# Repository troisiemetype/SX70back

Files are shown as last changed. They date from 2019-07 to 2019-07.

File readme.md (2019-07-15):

# SX70 back

## This Arduino sketch is for managing a SX70 instant film back.

The back is made of a SX70 which only the ejection mecanism was used.
It's included in a wooden enclosure made to fit a Busch Pressman C 3.5x4.5 press camera.

The mecanism includes motor, original switches, gear train. The shutter, bellows, mirror, and original enclosure has been removed, as well as the picture counter, which has been embbeded in the arduino program.

More informations about the functions, switches management, etc. in the .ino file.

### Be kind :

If you use this code and files for a project, consider letting me know, drop a line : lelabodu troisieme (at) gmail.com. Pictures will be welcome, and a donation as well ! :)

### About 3D files :

The STL for the back are included in the STL folder.

*Inner frame* is the only part to be 3D printed, all the enclosure is made of wood, and trigger button and door latch made of brass. They probably can be 3D printed too.

*Main shell* has holes for 3mm leds. On mine the small holes have been filed with clear PU resin.

*Door shell* is composed of several parts assembled, there is an inside slot for mounting a "light tongue", altough maybe not sctrictly necessary.

### About Arduino and electronics :

The flex circuit has been removed from the back chassis. Switches have been connected to ground, and to Arduino using internal pull-up resistors. S3 and S5 (see SX70 repair manual) are used to detect different ejections steps. S7 is the main power switch, which closes and powers the system when a pack is inserted and the door closed. The Arduino is powered as long as there is a pack, but is put asleep after 20 seconds (can be modified) idle.

An Arduino pro-mini has been used, it's placed in a 2mm thick recess in the inside of the main shell near the leds, and simply mounted with double-side tape

### The program uses two libraries :

#### Push button
https://github.com/troisiemetype/PushButton
Simplifies the switches and button management, by providing functions to update, debounce short and long clic, etc. Once a button / switch is created, it just have to be updated as soon as possible (polled in the main loop), and tested whenever needed)

#### Timer
https://github.com/troisiemetype/Timer
Timer made from millis() core Arduino function, with convenient functions for setting times, make loops, etc. Non blocking.

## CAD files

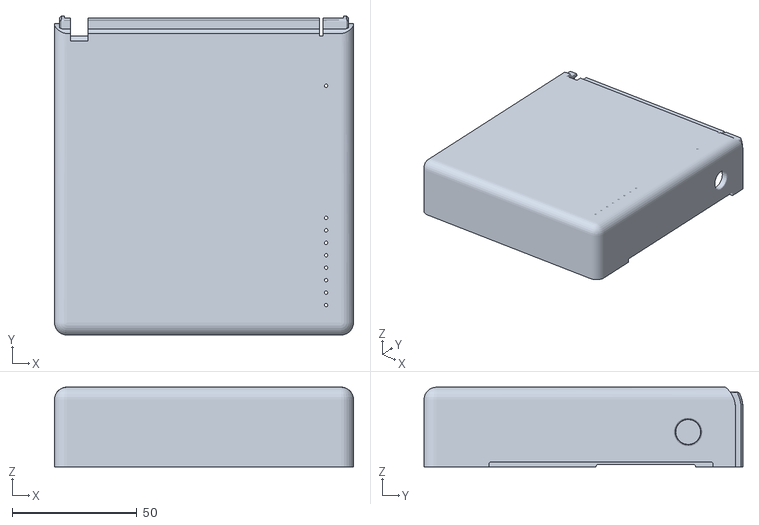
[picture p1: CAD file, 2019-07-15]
stl/pola - main shell.stl
120.0 x 128.0 x 32.0

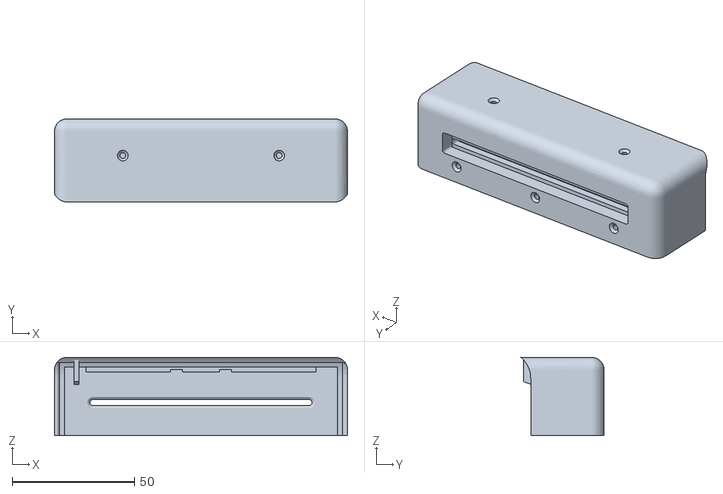
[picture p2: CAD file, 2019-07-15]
stl/pola - door shell.stl
120.0 x 34.0 x 32.0

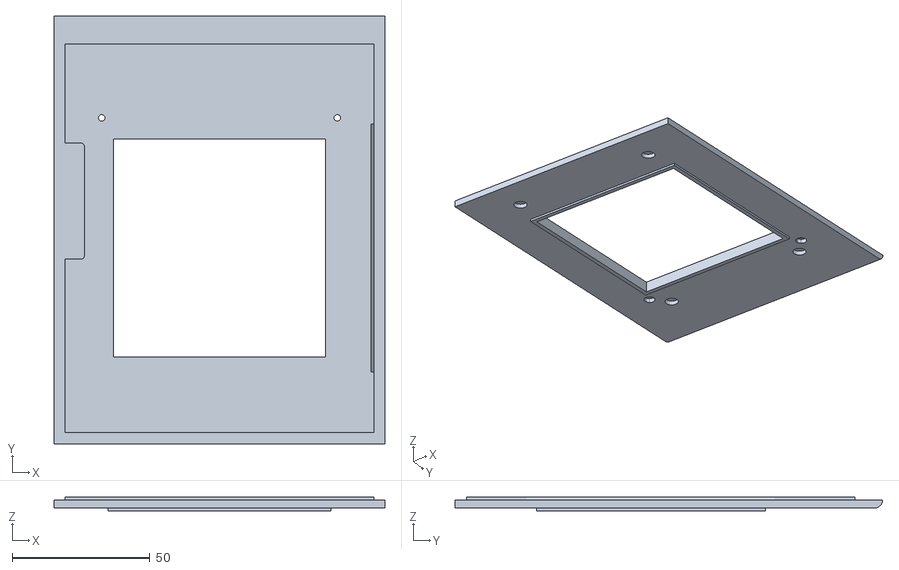
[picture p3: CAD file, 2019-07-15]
stl/pola - base.stl
120.0 x 155.0 x 5.00

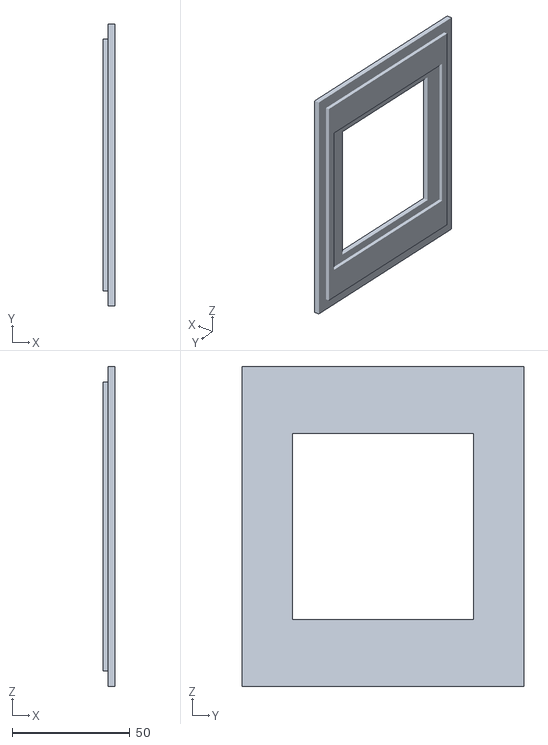
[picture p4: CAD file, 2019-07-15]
stl/pola - assise.stl
5.00 x 120.0 x 136.0

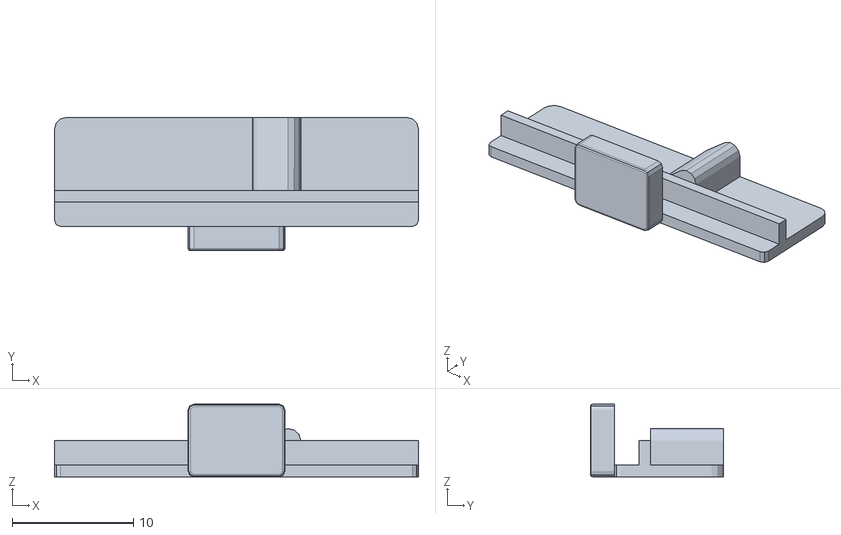
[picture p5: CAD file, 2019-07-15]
stl/pola - door slide.stl
30.0 x 11.0 x 6.00

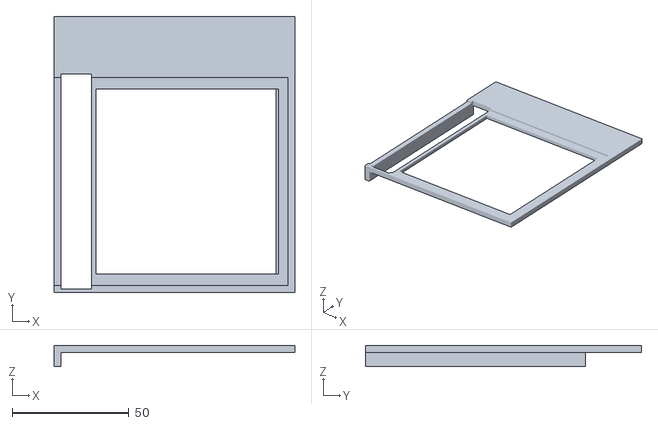
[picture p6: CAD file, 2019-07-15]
stl/Pola - inner shim.stl
103.0 x 118.0 x 9.00

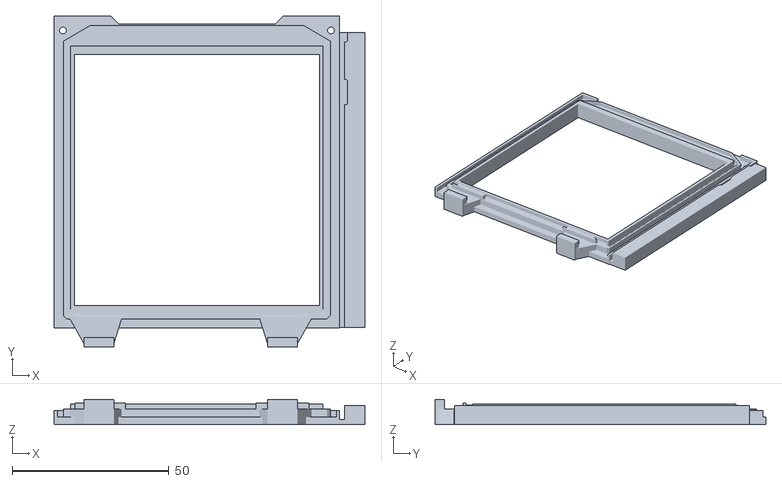
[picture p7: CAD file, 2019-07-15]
stl/pola - inner frame.stl
99.0 x 105.5 x 8.00

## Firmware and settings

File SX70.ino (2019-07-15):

/*
 * This program handles the ejection system of a modified polaroid SX70 instant camera
 * Copyright 2019 - Pierre-Loup Martin / le labo du troisième
 *
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
 * You should have received a copy of the GNU General Public License
 * along with this program.  If not, see <http://www.gnu.org/licenses/>.
 */

/*
 * This program handles the ejection system of a modified polaroid SX70 instant camera.
 * It is built around a state machine, and is using the original sensors of the original camera.
 *
 * Here is a list of the sensors :
 * S1	Shutter. Original sensor is crimped in the shutter unit, but a new one is used so the user can trigger the ejection process.
 * S2	Flash mode. In shutter unit, not used.
 * S3	Detects when the mirror is raised. useless as the mirror is removed, but used as a confirmation ejection has started.
 * S4	Solenoid sensor. Used in the camera to reduce power on the solenoid once the shutter is closed. Not used.
 * S5	Detects when the mirror is rearmed. used to stop the ejection process with ynamic braking of the motor.
 * S6	Main circuit power. Close when the camera is opened. Present, but not used.
 * S7	Main circuit power. Open when the front door is opened. Used as a general power-off switch.
 * S8	Closed when a new pack is inserted, then opened when the dark slide is ejected. Not used.
 * S9	Closed when counter reaches 0 (and the pack is empty). Not used.
 *
 * Here are a list of the IO of the system (all switches are internally pulled-up and active low):
 * S1	User-button.		PB0 / D8		Wake up the system out of sleep / triggers the ejection process.
 * S3	Mirror raised		PB1 / D9		Detects the ejection has started.
 * S5	Ejection ended		PB2 / D10		Stop the ejection process.
 * S7	Front door			main switch		Main switch.
 * 
 * motor					PB3 / D11		Run the motor through a mosfet transistor.
 *
 * bargraph					port D 			8 leds placed in a row, to display remaining pictures.
 *
 * status led 				PB5 / D13		Status led lit when awake. 
 *
 * Here is how the state machine works :
 * - When a new pack is inserted into the camera, and the front door is closed, current can flow into the circuit.
 * - The Arduino resets and initialize, sets the remaining pictures to 9 (8 pictures plus the dark slide).
 * 		Maybe the darkslide can be ejected by itself too.
 * - Then after 20 seconds, it goes to sleep, which is its "normal" mode.
 * - When the user needs to eject a film after having took a picture, the shutter (S1) is pressed.
 * - The system there goes out of sleep, displays the remaining views of the pack, and the sleep timer is launched.
 *		Note : as a safety mesure, S1 must be released before the state changes.
 * - When the shutter (S1) is pressed again, the motor runs, the ejection process starts, and the sleep timer is stopped.
 *		note : the shutter as a delay for long press, to avoid accidental film ejection.
 *		if the shutter is pressed for less than half a second (or other delay set), sleep counter start again.
 * - When S3 is trigerred, the system starts to monitor S5.
 * - When S5 is trigerred, the motors stops, the image counter is decremented, and the timer for sleep is re-launched.
 * - If the shutter is not pressed before the sleep timer is over, then the system goes to sleep again.
 */

// includes
#include <avr/sleep.h>

#include "PushButton.h"
#include "Timer.h"

const uint16_t SW1_LONG_DELAY = 500;			// Delay for a long press of the user button, us
const uint8_t TIMER_SLEEP_DELAY = 20;			// timer delay before sleep, seconds.

// Picture counter init.
uint8_t pictureCounter = 9;
uint8_t pictureByte = 60;
uint8_t pictureLoop = 0;

bool statusLed = 0;

// pin definition
const uint8_t PIN_SW1 = 9;
const uint8_t PIN_SW3 = 10;
const uint8_t PIN_SW5 = 11;
const uint8_t PIN_MOTOR = 12;
const uint8_t PIN_STATUS_LED = 13;

// No pin definition for bargraph, as it is initialised in a loop, and set with direct port D manipulation.

// switches definition
PushButton sw1 = PushButton();
PushButton sw3 = PushButton();
PushButton sw5 = PushButton();

// Timer
Timer timerSleep = Timer();
Timer timerProcess = Timer();
const uint8_t TIMER_PROCESS_DELAY = 50;		// timer delay for led blking when processing, milliseconds.

// Definition of the states used for different phases of work.
enum state_t{
	WAKE_UP = 0,
	WAIT_SW1,
	IDLE,
	EJECT_START,
	EJECT_WAIT_SW3,
	EJECT_WAIT_SW5,
	EJECT_STOP,
} state;

// initialisation at power up, i.e. when a new pack is inserted.
void setup(){
	// Init buttons
	sw1.begin(PIN_SW1, INPUT_PULLUP);
	sw1.setLongDelay(SW1_LONG_DELAY);
	sw3.begin(PIN_SW3, INPUT_PULLUP);
	sw5.begin(PIN_SW5, INPUT_PULLUP);

	timerSleep.init();
	timerProcess.init();

	// Outputs
	// led bargraph
	for(uint8_t i = 0; i < 8 ; ++i){
		pinMode(i, OUTPUT);
	}
	// Status led
	pinMode(PIN_STATUS_LED, OUTPUT);
	// Motor
	pinMode(PIN_MOTOR, OUTPUT);

	// disable ADC
	ADCSRA &= ~(1 << ADEN);

	// disable all the functions not used by the program.
	// TWI
	// Timer 2
	// Timer 1
	// SPI
	// USART
	// ADC
	PRR |= (1 << PRTWI) | (1 << PRTIM2) | (1 << PRTIM1) | (1 << PRSPI) | (1 << PRUSART0) | (1 << PRADC);

	state = WAKE_UP;

//	wakeUp();

	// For debuging : display the value of Power Reduction Register
//	displayPort(PRR);
}

void loop(){
	if (timerSleep.update()) goToSleep();

	// These few lines are for led diming. pictureLoop is incremented at each loop,
	// And leds are lit only when it is 0. Kind of pwm, main goal is to save energy from battery.
	if (pictureLoop == 0){
		PORTD = pictureByte;
		digitalWrite(PIN_STATUS_LED, statusLed);

	} else {
		PORTD = 0;
		digitalWrite(PIN_STATUS_LED, 0);
	}

	// Here we increment loop (trivial), and reset it when it goes above 7
	++pictureLoop;
	// value can be changed, but MUST be a power of 2 minus 1 ((2^x) - 1)
	pictureLoop &= 7;

	sw1.update();
	sw3.update();
	sw5.update();

	// State machine for dispatching to main functions following current state.
	switch(state){
		case WAKE_UP:
			wakeUp();
			state = WAIT_SW1;
			break;

		case WAIT_SW1 :
			if (sw1.isReleased()){
				state = IDLE;
				timerSleep.setSeconds(TIMER_SLEEP_DELAY);
				timerSleep.start();
			}
			break;

		case IDLE :
			if (sw1.isLongPressed()){
				timerSleep.stop();
				timerProcess.setDelay(TIMER_PROCESS_DELAY);
				timerProcess.start(-1);
				
				digitalWrite(PIN_MOTOR, 1);
				state = EJECT_WAIT_SW3;
			} else if (sw1.justReleased()){
				timerSleep.start();
			}
			break;

		case EJECT_START :
			break;

		case EJECT_WAIT_SW3 :
			if(timerProcess.update()) statusLed ^= 1;
			if (sw3.isReleased()) state = EJECT_WAIT_SW5;
			break;

		case EJECT_WAIT_SW5 :
			if(timerProcess.update()) statusLed ^= 1;
			if (sw5.isPressed()){
				digitalWrite(PIN_MOTOR, 0);
				timerProcess.stop();

				if(pictureCounter !=0) pictureCounter--;
				pictureByte = 0;
				for (uint8_t i = 0; i < pictureCounter; ++i){
					pictureByte |= (1 << i);
				}

				state = WAKE_UP;
			}
			break;

		case EJECT_STOP :
			break;

		default:
			break;
	}

//	if (sw1.isLongPressed()) eject();
	
}

// Initialisation when waking up, i.e. when the user pushes the button.
void wakeUp(){

	statusLed = 1;
	digitalWrite(PIN_MOTOR, 0);

	// We turn pullup on on wake up, as it is disabled when asleep.
	sw3.begin(PIN_SW3, INPUT_PULLUP);
	sw5.begin(PIN_SW5, INPUT_PULLUP);


//	displayPictureCount();
/*
	// check for button being depressed to avoid accidental picture ejection.
	for(;;){
		sw1.update();
		if (sw1.isReleased()) break;
	}

	timerSleep.setSeconds(TIMER_SLEEP_DELAY);
	timerSleep.start();
*/
}

// Start ejection sequence
// Motor started.
// S3 triggered confirms ejection is running.
// S5 trigerred confirms ejection is finished.
// Motor stopped.
// Picture counter decremented.
// Sleep timer relaunched.
/*
void eject(){
	timerSleep.stop();
	
	timerProcess.setDelay(TIMER_PROCESS_DELAY);
	timerProcess.start(-1);
	
	digitalWrite(PIN_MOTOR, 1);

	for(;;){
		if(timerProcess.update()){
			statusLed ^= 1;
			digitalWrite(PIN_STATUS_LED, statusLed);
		}

		sw3.update();
		sw5.update();
		if (sw3.isReleased()) break;
	}

	for(;;){
		if(timerProcess.update()){
			statusLed ^= 1;
			digitalWrite(PIN_STATUS_LED, statusLed);
		}
		
		sw3.update();
		sw5.update();
		if (sw5.isPressed()) break;
	}

	digitalWrite(PIN_MOTOR, 0);

	timerProcess.stop();

	if(pictureCounter !=0) pictureCounter--;
	for (uint8_t i = 0; i < pictureCounter; ++i){
		pictureByte |= (1 << i);
	}

	wakeUp();

}
*/

void displayPictureCount(){
	uint8_t output = 0;
	if (pictureCounter == 9){
		// 60 is 0b00111100.
		// It displays the four leds in the center as a remainder the dark slide is still here.
		output = 60;
// Finally not used : when pack is empty, counter is off. But pictures can still be processed.
// usefull if ones uses vintage polaroid film, which packs are ten views.		
//	} else if (pictureCounter == 0){
//		output = 36;
	} else {
		for (uint8_t i = 0; i < pictureCounter; ++i){
			output |= (1 << i);
		}
	}

	PORTD = output;

}

// For debugging purpose : use the eight leds to display the state of a register or any other byte data.
void displayPort(uint8_t data){
	PORTD = data;
	delay(3000);
	displayPictureCount();
}

void goToSleep(){
	// Set an interrupt ont PCINT1 (pin 9 / port B1 ) to wakeup.
	PCICR = (1 << PCIE0);
	PCMSK0 = (1 << PCINT1);

	// disable picture count
	PORTD = 0;
	// disable status led
	digitalWrite(PIN_STATUS_LED, 0);

	// disable pullup for sleep on the ejection switches.
	sw3.begin(PIN_SW3, INPUT);
	sw5.begin(PIN_SW5, INPUT);

	// Store the register values.
	char sregTemp = SREG;

	//enable sleep, set power down mode
	SMCR |= (1 << SE);
	SMCR |= (1 << SM1);

	// Disable watchdog timer
	WDTCSR = 0;
	
	// Disable Brown Out detector
	// (the datasheet gives this way of proceeding)
	MCUCR |= (1 << BODSE) | (1 << BODS);
	MCUCR |= (1 << BODS);
	MCUCR &= ~(1 << BODSE);
	
	//	set_sleep_mode(SLEEP_MODE_PWR_DOWN);
	sleep_mode();

	//disable sleep
	SMCR &= ~(1 << SE);

	//Restore status register
	SREG = sregTemp;

	//reinit devices
	state = WAKE_UP;
//	wakeUp();
}

ISR(PCINT0_vect){
	//clear the interrupts, are they are only for sleep wakeup.
	PCICR = 0;
	PCMSK0 = 0;

}

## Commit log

2019-07-15 Modified Idle state with justreleased test for button, so the sleep timer is relaunched if short-clicked. Added STL for back parts. Modified readme.
    [Pola - inner shim.stl, pola - assise.stl, pola - base.stl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]
2019-07-15 Errors in readme
    [pola - inner frame.stl]
2019-07-15 When there is no modifications left to do, ther still modifications left to do ! :) Corrected licence and added remark about Arduino board mounting.
    [SX70.ino]

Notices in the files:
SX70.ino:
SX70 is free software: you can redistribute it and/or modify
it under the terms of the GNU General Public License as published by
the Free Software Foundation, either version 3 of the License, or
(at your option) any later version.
